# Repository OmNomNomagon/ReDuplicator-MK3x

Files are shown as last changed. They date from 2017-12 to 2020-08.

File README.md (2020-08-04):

This project is a complete overhaul of the original Wanhao i3 with a few main objectives:
- Keep the core components of the printer while upgrading its structure.  
- Create maximum rigidity through a sturdy 3030 Aluminium extrusion frame. 
- Allow for future proofing and commonality of parts by basing all printed parts on the current Original Prusa MK3 files. 
- Reduce the weight of the X and Y carriages where possible to improve print speed and quality.

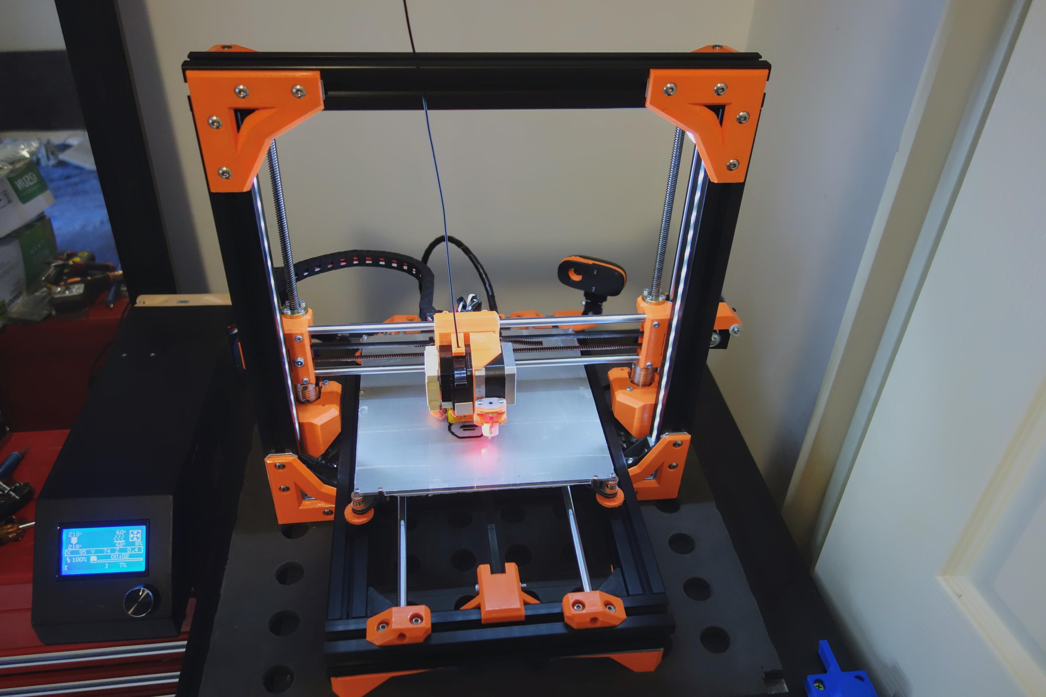
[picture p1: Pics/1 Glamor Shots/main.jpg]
noooice
 

The Wanhao i3 is a fabulous printer, but new generations of printers have begun pushing the boundaries. It has become apparent that in comparison, the Wanhao has a few deficiencies. Deficiencies which we will address in this project. The key improvements of this upgrade include:
- Much better rigidity through 3030 extrusions and metal brackets. Even with my or Azza’s excellent z braces the printer was still susceptible to slight wobble, especially under twisting forces (pull left tower and push right tower). When moving the printer it would require constant releveling due these small movements. Now i can barely get any movement using my full strength. 
- Comfortably increase Z height to ~200mm
- Reduce noise. By not screwing the motors directly onto the metal frame, motor vibrations and noise is reduced significantly. 
- Move towards more standard Prusa files for future upgradability, but with added strength improvements.
- Modular hotend, This design allows for the hotend to be replaced easily replaced without disassembling the printer. I have created a Titan Aero mount as an alternative to the original MK10 with a E3DV6 mount incoming.
- Sturdier 4 bearing Prusa style X-gantry. Not sure if it was specific to my printer or a common Wanhao problem, but my X gantry always had a lot of wobble which may have been a source of printing artifacts.  
- Noticeably better print quality due to a combination of everything above. I am able to print faster with better quality.
- All Wanhao i3 variants and rebrands are compatible, however the plus will require additional work to create an enclosure for the electronics. This project can also be built from scratch, or salvaged from other printers as long as measurements are altered accordingly. 

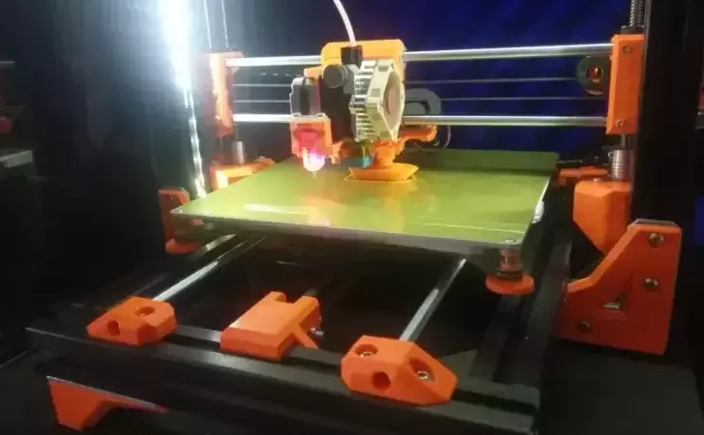
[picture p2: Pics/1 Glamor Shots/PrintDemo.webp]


Sample Print @~100mm/s on the titan aero extruder.

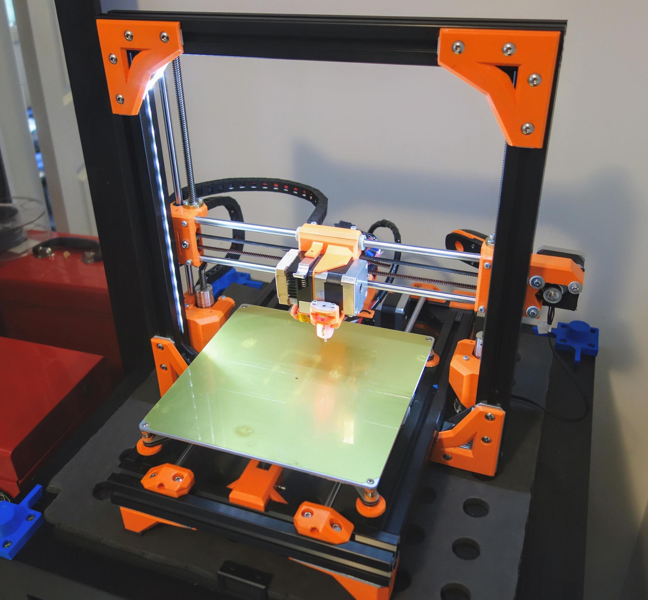
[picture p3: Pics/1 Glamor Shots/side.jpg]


Sample of improved print quality. 0.24mm layer height @ 70mm/s (titan aero).

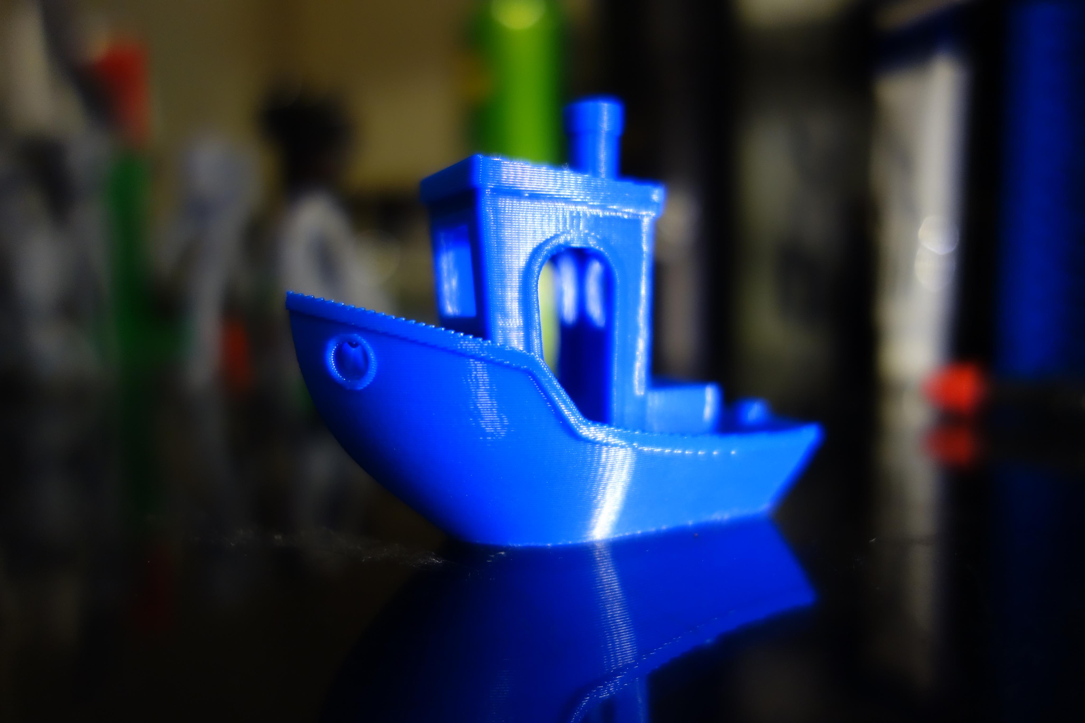
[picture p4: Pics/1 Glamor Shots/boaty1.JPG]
boatyMcboat


This project will be maintained both at [github](https://github.com/OmNomNomagon/ReDuplicator-MK2sx) and at [thingiverse](https://www.thingiverse.com/thing:2686588). The files were created using a combination of Fusion360 and tinkercad. They can be viewed and edited via [this Tinkercad link.](https://www.tinkercad.com/things/azPlfmHU5MQ#/)  

## Table Of Contents

- [1. Bill Of Materials](https://github.com/OmNomNomagon/ReDuplicator-MK2sx/wiki/1.--Bill-Of-Materials)
- [2. Printing Parts & Pre Assembly](https://github.com/OmNomNomagon/ReDuplicator-MK2sx/wiki/2.-Printing-Parts-&-Pre-Assembly)
- [3. Base](https://github.com/OmNomNomagon/ReDuplicator-MK2sx/wiki/3.-Base)
- [4. Begin The ZTower](https://github.com/OmNomNomagon/ReDuplicator-MK2sx/wiki/4.-Begin-The-ZTower)
- [5.1 Hotend MK10 Original](https://github.com/OmNomNomagon/ReDuplicator-MK2sx/wiki/5.1-Hotend-MK10-Original)
- [5.2 Hotend Titan Aero Upgrade](https://github.com/OmNomNomagon/ReDuplicator-MK2sx/wiki/5.2-Hotend-Titan-Aero-Upgrade)
- [5.3 Hotend E3D Hemera Upgrade](https://github.com/OmNomNomagon/ReDuplicator-MK3x/wiki/5.3-Hotend-Hemera-upgrade)
- [6. XAxis Gantry](https://github.com/OmNomNomagon/ReDuplicator-MK2sx/wiki/6.-XAxis-Gantry)
- [7. Complete the ZTower](https://github.com/OmNomNomagon/ReDuplicator-MK2sx/wiki/7.-Complete--the-ZTower)
- [8. YAxis](https://github.com/OmNomNomagon/ReDuplicator-MK2sx/wiki/8.--YAxis)
- [9. Cabling](https://github.com/OmNomNomagon/ReDuplicator-MK2sx/wiki/9.-Cabling)
- [9.1. Recommendations & Future Dev](https://github.com/OmNomNomagon/ReDuplicator-MK2sx/wiki/9.1.-Recommendations-&-Future-Dev)

## Thanks and Acknowledgements
- [Prusa Research MK2s](https://github.com/prusa3d/Original-Prusa-i3) 
- [Datvr's Prusa MK2S-x](https://www.thingiverse.com/thing:1692666)
- [Thorped's excellent Wanhao Fan Duct ](https://www.thingiverse.com/thing:1246425)
- [Cyul's spool holder](https://www.thingiverse.com/thing:1635585)

## Changelog
1.0 - Initial Release

1.01 - Updated idler files with multiple z endstop mount points for upcoming Titan Aero upgrade. Sturdier cable cover box. Added 1Meter GT2 belt to BOM as the stock belt may not be long enough (can anyone confirm?)

1.02 - Updated the **Part Fan Bracket** to **Part Fan Bracket V1.1** The original doesn't align with the carriage plates properly. Please print the revised one.

1.03 - Uploaded a new Y Carriage Belt Holder. This one is based on the current MK3 design and is much easier to fix and tension.

1.04 - **X Gantry Idler 9MM V2** was missing the heat-sert insert holes to mount the cable box. Updated and fixed with **X Gantry Idler 9MM V3**. If you have already printed V2, you can keep the part and manually drill 2x 4mm holes spaced 9mm wide and 6mm deep.

1.1 - 11/03/2018 Major Prusa MK3 Update. This updates an update of many of the original MK2s based parts to MK3 Based parts. This includes;

  - MK3 Based Part Cooling shroud and mount. It performs much better than the original Thorped based one. flawless @60 degree overhang with some sagging @70 degree overhang. The original would show artefacts [@60 degrees.](https://raw.githubusercontent.com/OmNomNomagon/ReDuplicator-MK2sx/master/Pics/9%20Titan/overhang.jpg). Almost comparable to the [Dii Cooler.](https://www.reddit.com/r/3Dprinting/comments/7kexdv/a_nearly_comprehensive_study_of_cooling_fans_and/) 

  - Much improved X Carriage. This uses the new [MK3 belt mounting method](https://raw.githubusercontent.com/OmNomNomagon/ReDuplicator-MK2sx/master/Pics/4%20Hotend/CarriageNew.jpg) which is much easier to install under tension. The whole extruder assembly can now also easily slide on and off the rods to greatly simplify installation and maintenance. 16mm M3 screws are used to secure the bearings. I've also made and tested changes which allow the extruder assembly to be built without heat-serts and can be substituted with M3 nylocks. NOTE: due to these changes the Rear carriage plate is NOT compatible with the existing Front extruder plate as the hole spacing has been changed. The New Front extruder plate must be used.

  - Front Extruder Plate. Better spacing around the hotend to improve the filament path. Updating Hole Spacing to be compatible with the new Rear Carriage Plate. Strengthened BLTouch mount. Increase spacing around heater block to reduce residual heat. Not compatible with old extruder plate.

  - X Axis Motor Mount. Incorporates the new MK3 design. Better Spacing to ensure a straighter belt path. Includes new MK3 tensioner to easily tension X belt. Requires M3nS Nut and 20mm M3 screw. (Enough tension can be applied by without the M3nS) Installation is similar to the Prusa instructions [here, steps 11-18.](http://manual.prusa3d.com/Guide/4.+Z-axis+assembly/509?lang=en)

  - As this project  contains dozens of files already, Older retired files are retired to the [Retired Versions directory in github](https://github.com/OmNomNomagon/ReDuplicator-MK2sx/tree/master/STLs%20Reduplicator%20Core%20Parts/Retired%20Versions)
  
1.1.1 - Endstop Part For sensorless homing with TMC2130 Drivers.

1.2 - 05/11/2018 - Multiple improvements based on Prusa MK3 R3 release. This includes:

  - Prusa MK3 R3 based part cooling shroud. This gives a noticeable improvement over the original shroud. Also improved the clearance between the shroud and the nozzle.

  - Improved X Carriage rear plate. This was strengthend to better handle bumps and knocks. Rigidity is also improved. It is still a common part between the MK10 and titan aero extruders. 

  - Strengthened Z Rod Securer parts. Some people had issues with these snapping in PLA but should no longer be an issue.

1.3 - 17/02/2020 - E3D Hemera mount. Updated fan duct to the most recent R4 release. Added an angle for increased rear fan duct clearance. This will filter down to the other hotend designs shortly. Initial update of parts across to fusion 360. A number of parts have been converted and this will continue over time.

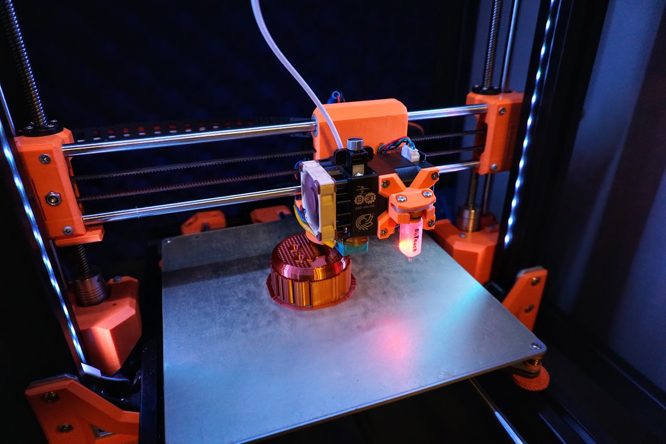
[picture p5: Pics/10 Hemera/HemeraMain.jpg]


Improved cable mounting system by clipping onto the X axis motor

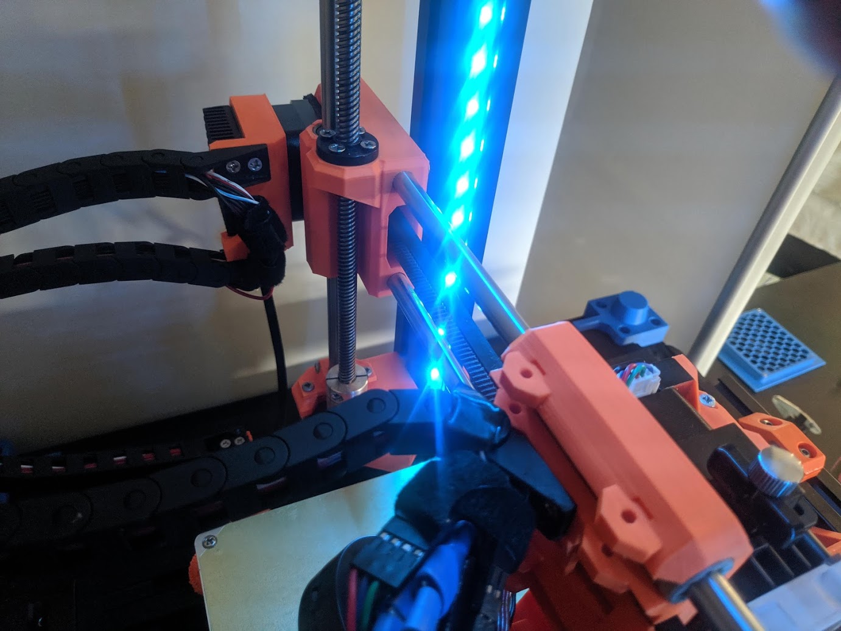
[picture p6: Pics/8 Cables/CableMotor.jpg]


1.3.1 - 19/02/2020 - MK52 Removeable heatbed Mod - resized rods and extrusions to accommodate the prusa MK3 heatbed.

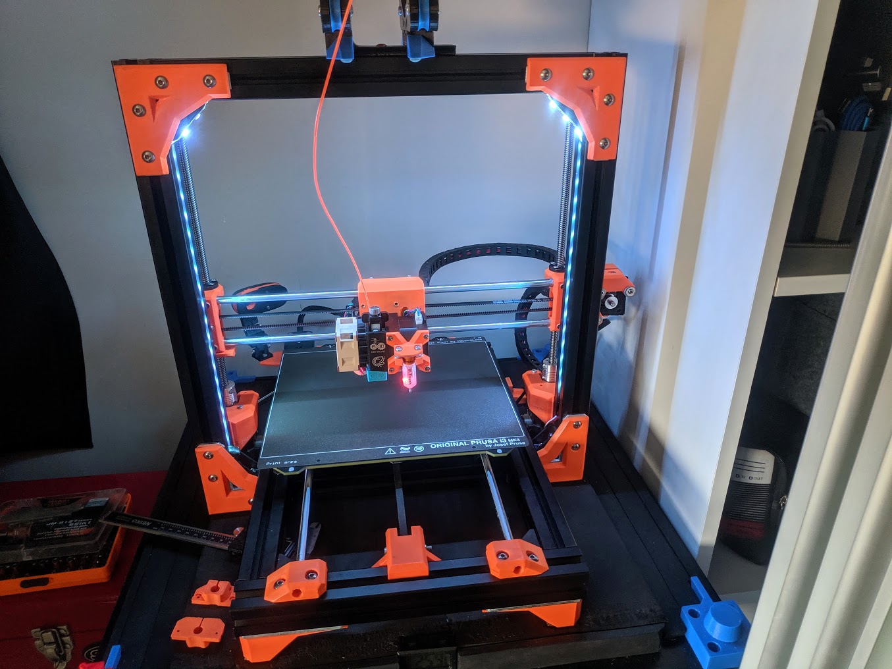
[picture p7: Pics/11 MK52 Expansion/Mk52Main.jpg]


1.4 - 05/08/2020 - Mk52 and Hemera Parts update. Significantly improved X idler, tensioner and motor holder, new Z Rod Holder design for much easier installations and accuracy. Improved Hemera fan shroud with improved airflow. Continued conversion from tincercad to F360 parts. These changes will filter down to the original reduplicator parts.

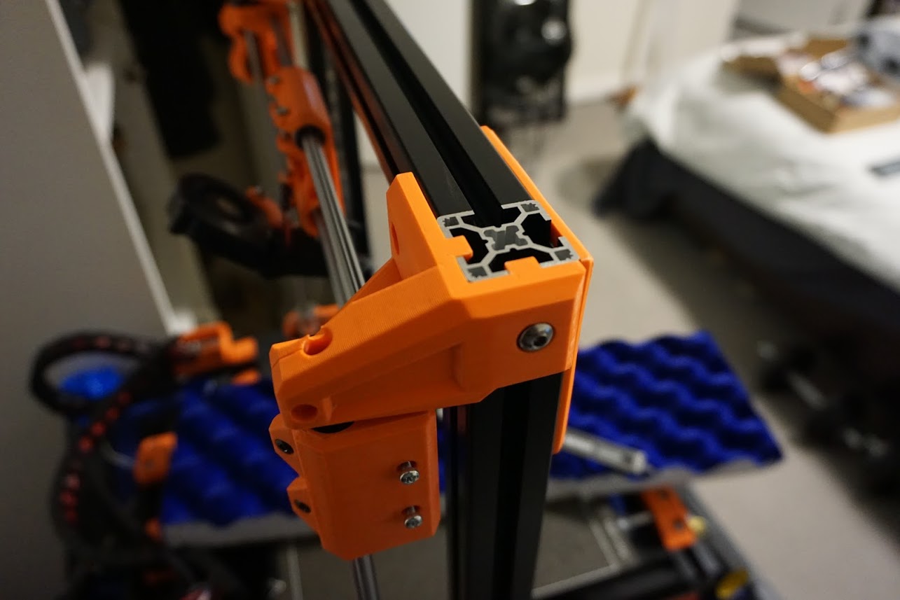
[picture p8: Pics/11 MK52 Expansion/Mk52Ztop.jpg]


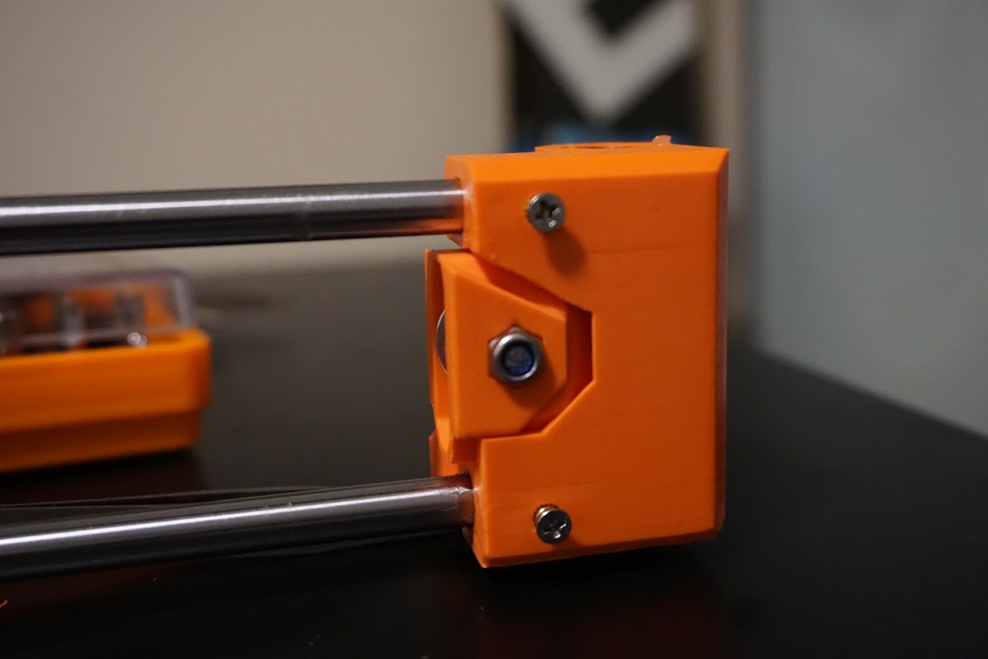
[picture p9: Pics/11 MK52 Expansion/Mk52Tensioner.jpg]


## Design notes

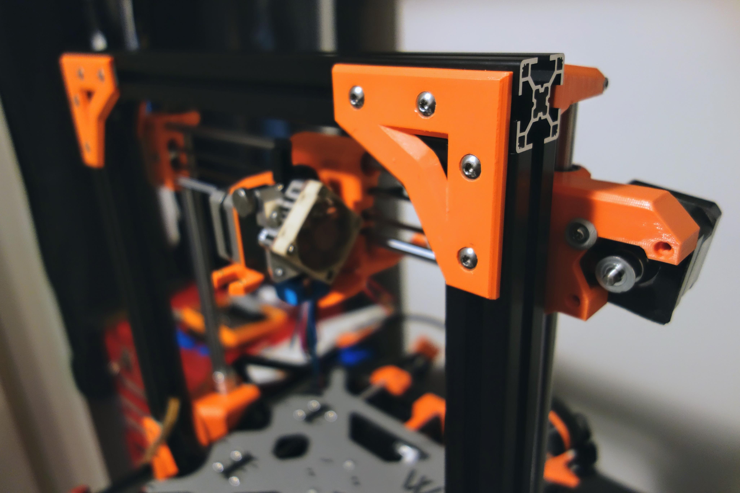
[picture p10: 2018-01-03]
Pics/5 Gantry/XGantryMotor.JPG

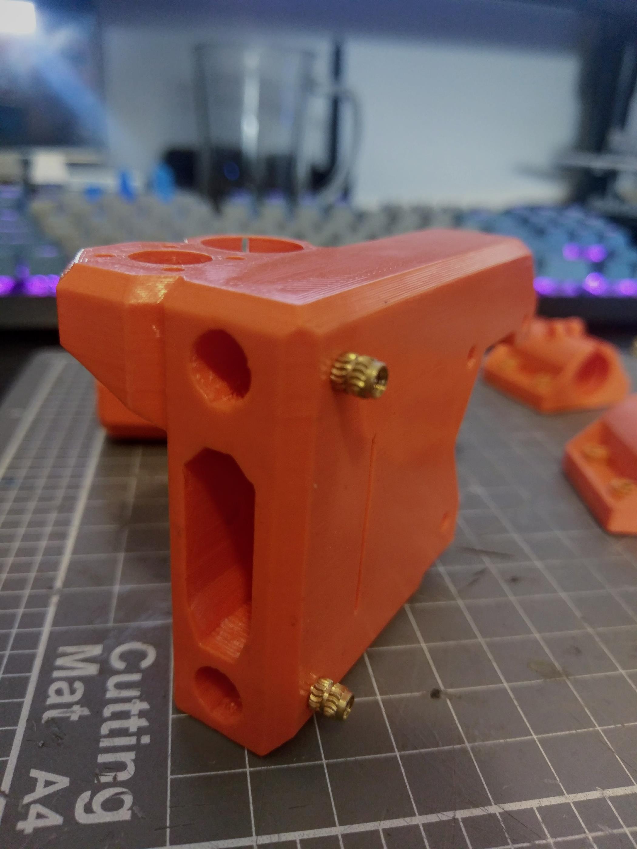
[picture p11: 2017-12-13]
Pics/5 Gantry/HeatSert1.jpg

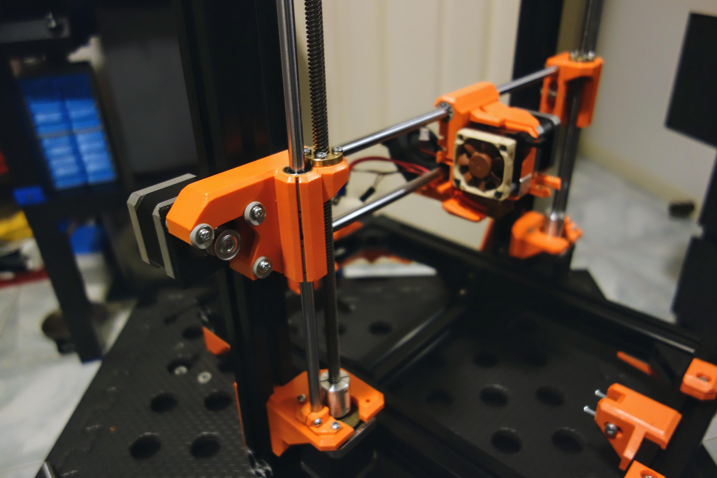
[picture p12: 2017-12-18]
Pics/1 Glamor Shots/ReversedEG.JPG

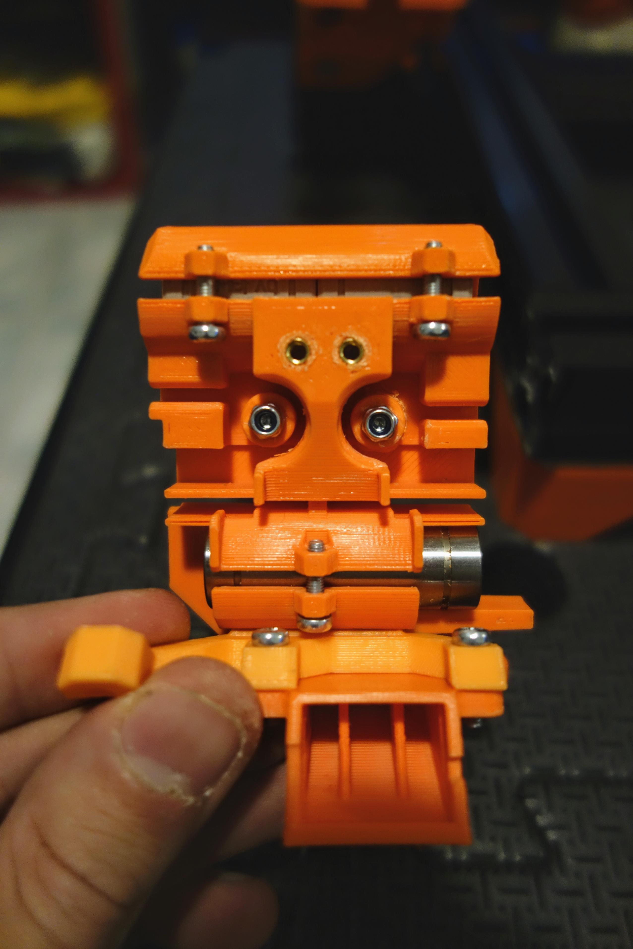
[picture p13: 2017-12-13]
Pics/4 Hotend/Fan2.jpg

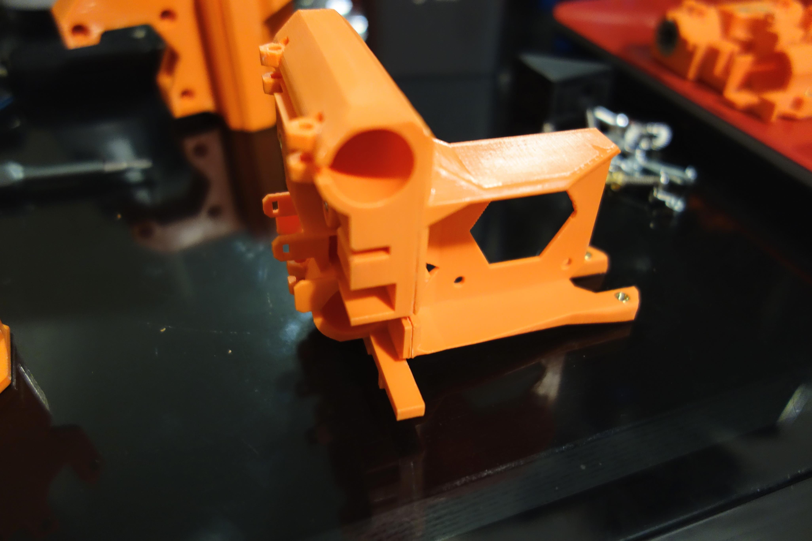
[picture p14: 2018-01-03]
Pics/9 Titan/TitanPart.JPG

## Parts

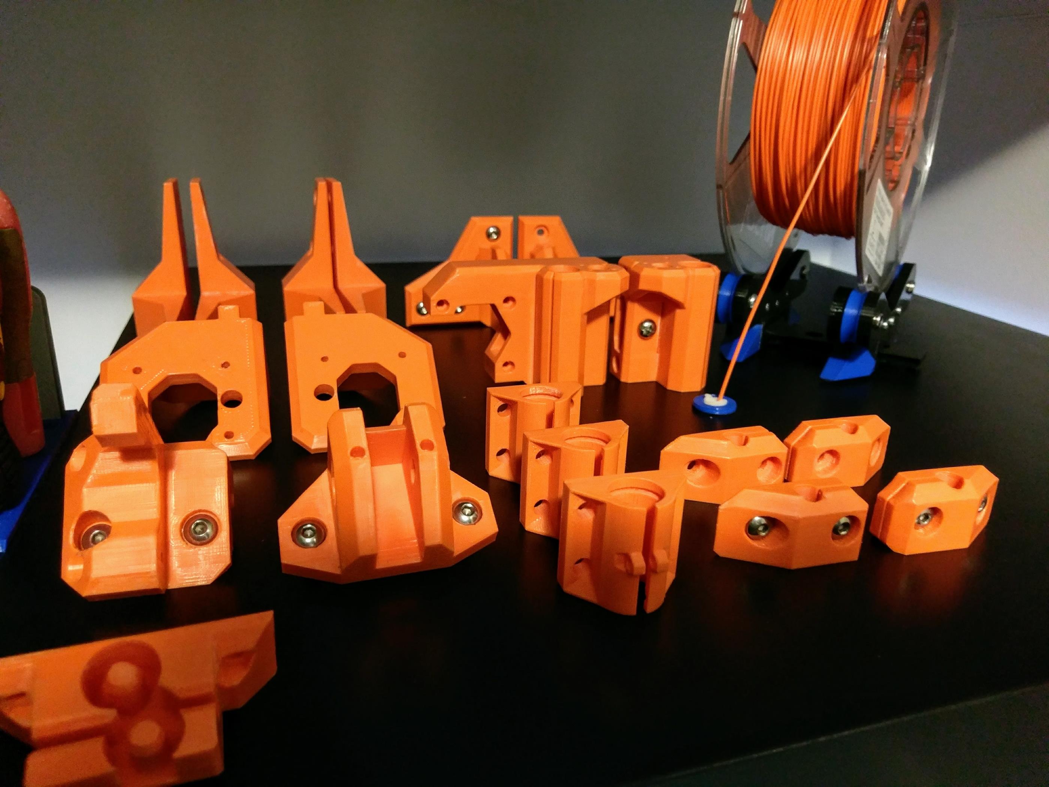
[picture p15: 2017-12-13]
Pics/2 Bottom Frame/Parts.jpg

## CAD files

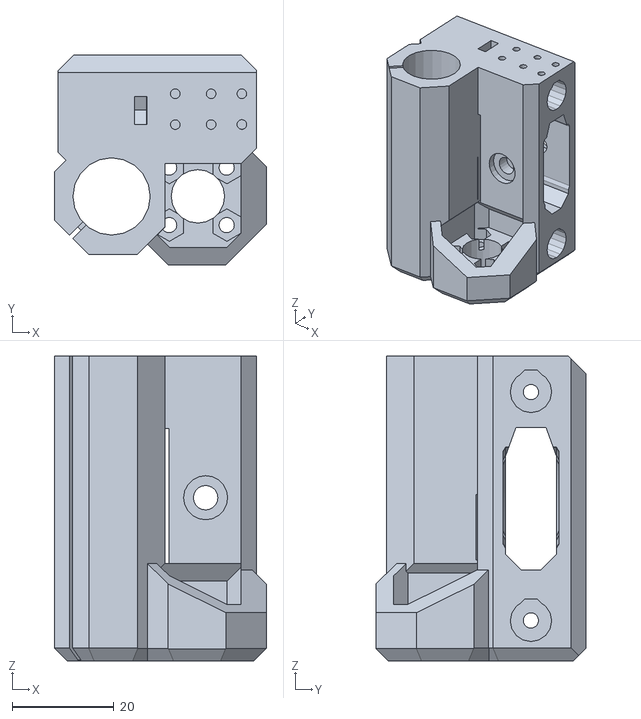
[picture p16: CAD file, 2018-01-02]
STLs Alternative & Optional/X Gantry Idler 11mm (Stock idler) V2.stl
41.7 x 41.4 x 60.0

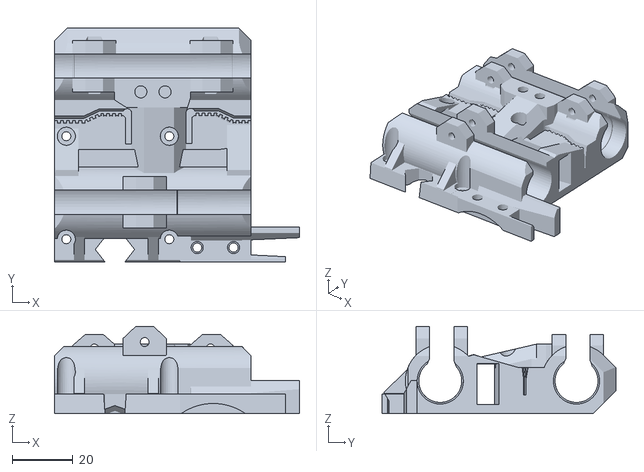
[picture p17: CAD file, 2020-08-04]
STLs E3D Hemera Hotend upgrade/Hemera X Carriage 360 V2.stl
80.9 x 77.2 x 28.8

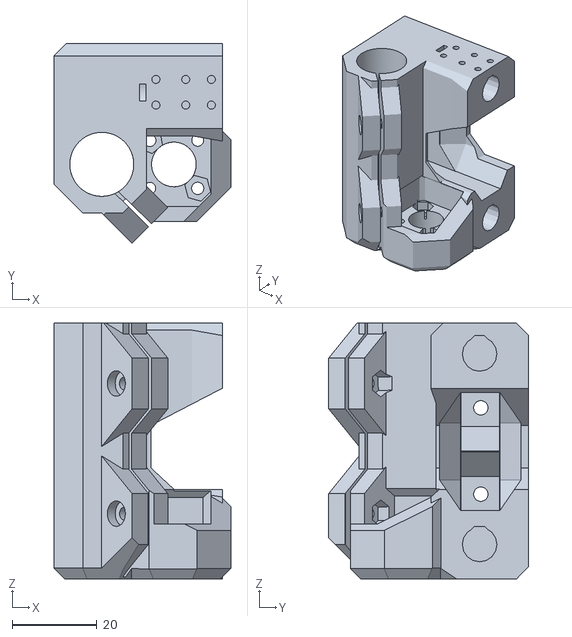
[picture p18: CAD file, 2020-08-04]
STLs MK52 Heatbed Expansion Upgrade/X Gantry Idler - MK52 Expansion 360 v2.stl
41.7 x 47.1 x 60.5

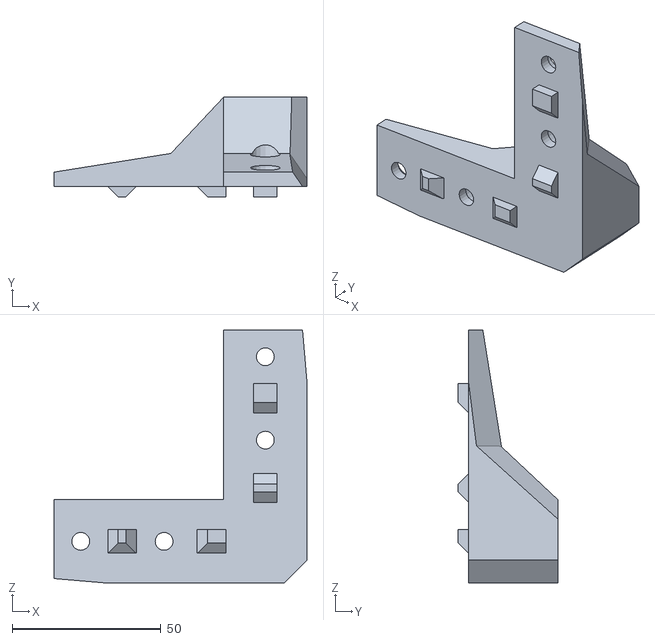
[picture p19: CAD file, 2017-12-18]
STLs Non Metal Tabbed Brackets/Leg H30.00 - Non Metal Tabbed X4.stl
85.0 x 33.5 x 85.0

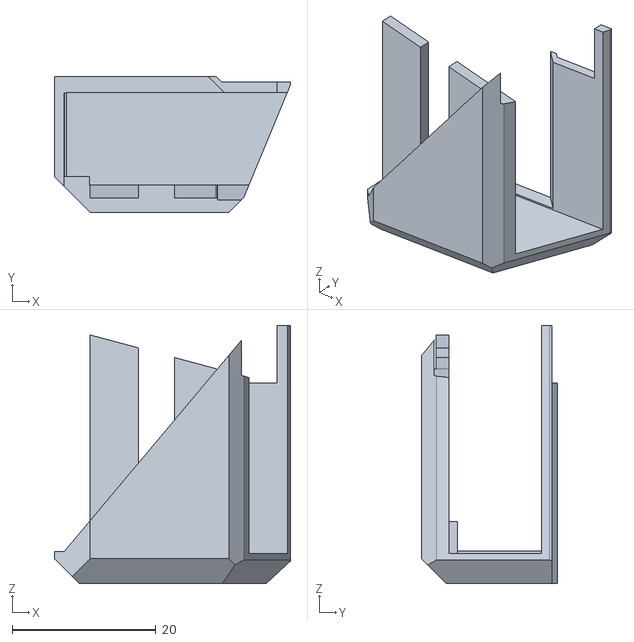
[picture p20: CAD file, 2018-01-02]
STLs Reduplicator Core Parts/Alternative Parts/X Gantry Cable Box Cover V2.stl
32.9 x 18.9 x 35.9

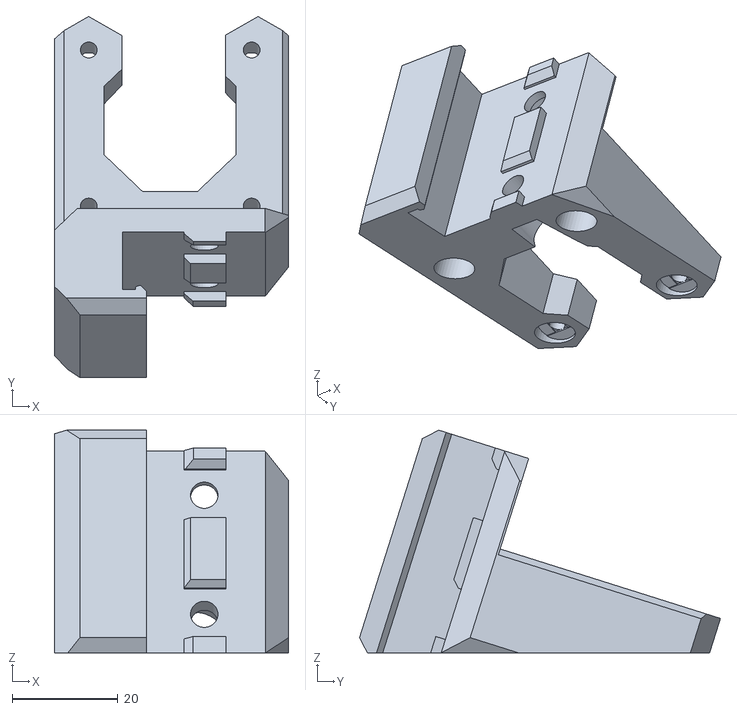
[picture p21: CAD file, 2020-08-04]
STLs Reduplicator Core Parts/Y Axis Motor Mount V3 360.stl
44.4 x 68.4 x 42.2

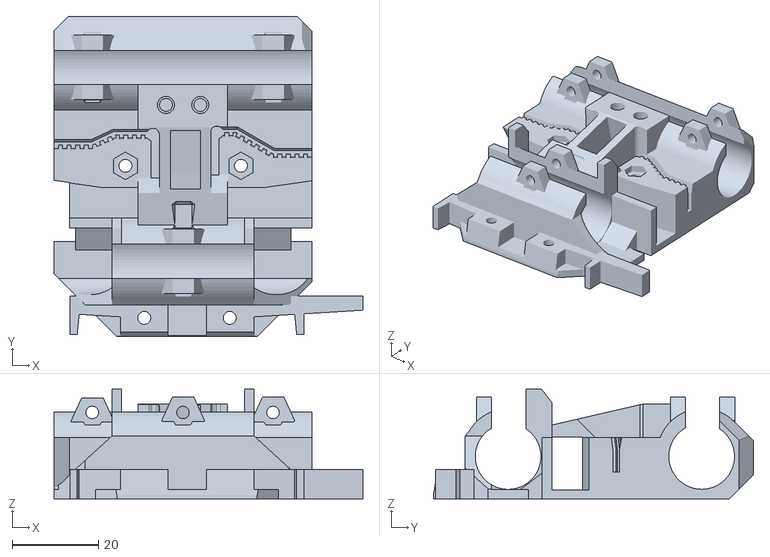
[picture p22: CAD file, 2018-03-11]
STLs Titan Aero Conversion/X Carriage Rear Bearing Plate MK3 V2.stl
71.8 x 74.4 x 25.5

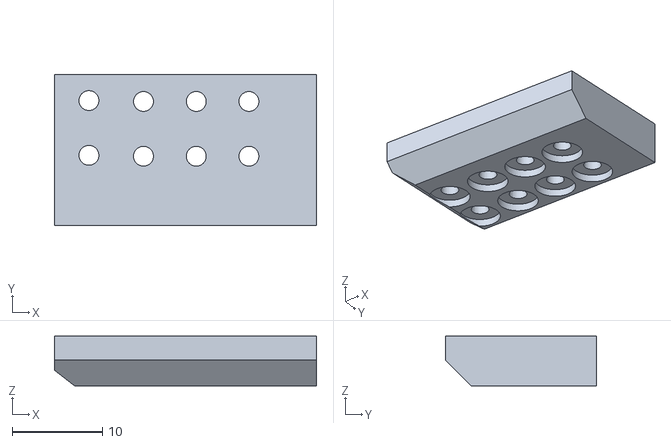
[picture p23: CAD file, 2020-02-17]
STLs Titan Aero Hotend Upgrade/X Axis TMC2130 Sensorless Endstop 360.stl
29.0 x 16.7 x 5.50

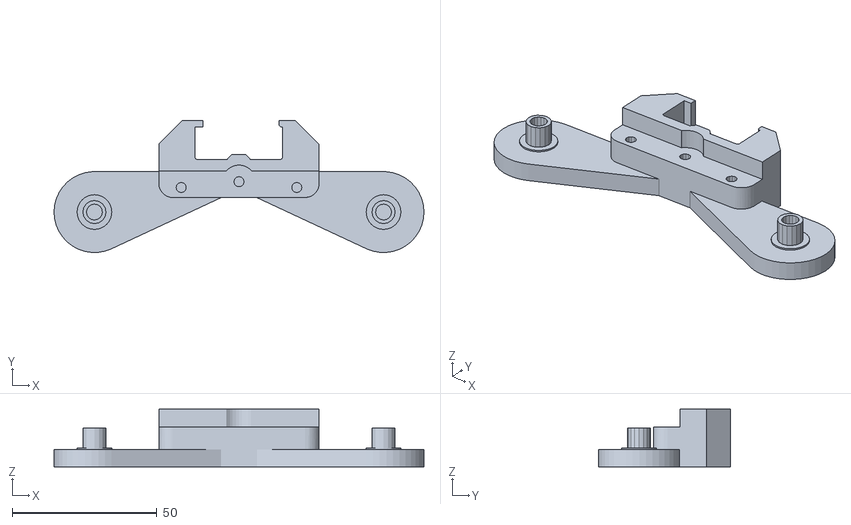
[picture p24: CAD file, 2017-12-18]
STLs Alternative & Optional/Top Mount Spool Holder Right.stl
128.0 x 45.6 x 20.0

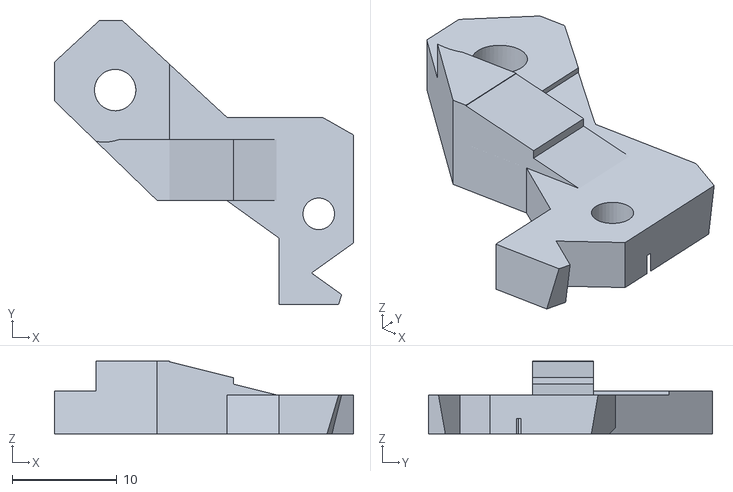
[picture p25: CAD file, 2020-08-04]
STLs E3D Hemera Hotend upgrade/Hemera Fan Mount V2 360.stl
28.6 x 27.1 x 6.93

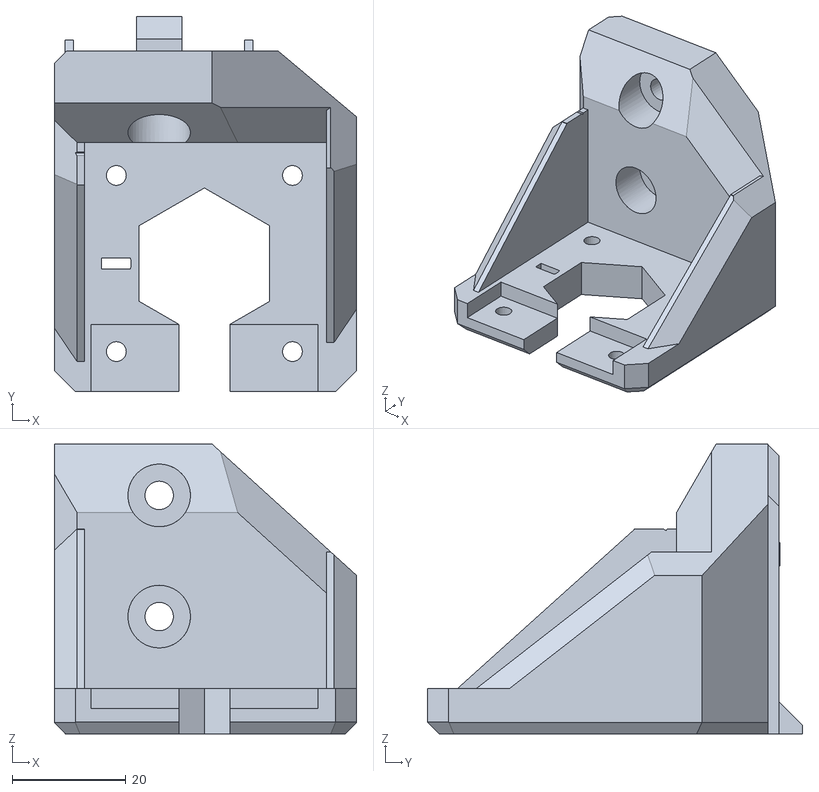
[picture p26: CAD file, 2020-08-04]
STLs MK52 Heatbed Expansion Upgrade/Z Axis Motor Bottom Left - MK52 Expansion 360 v2.stl
53.2 x 66.0 x 51.0

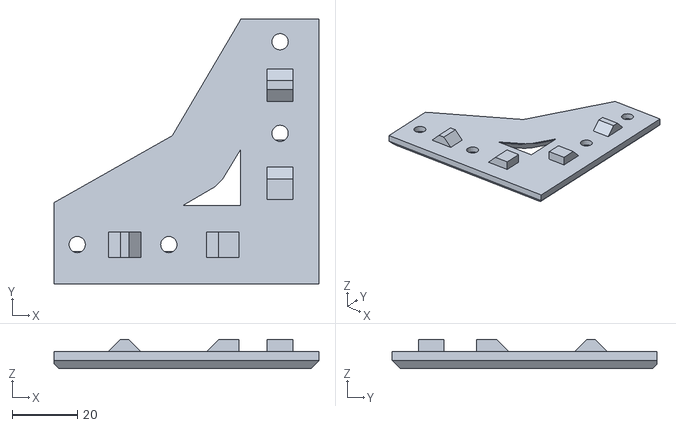
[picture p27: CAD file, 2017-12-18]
STLs Non Metal Tabbed Brackets/Tower Corner Bracket Large 80x80x5 V1 - Non metal Tabbed X2.stl
81.0 x 80.9 x 8.90

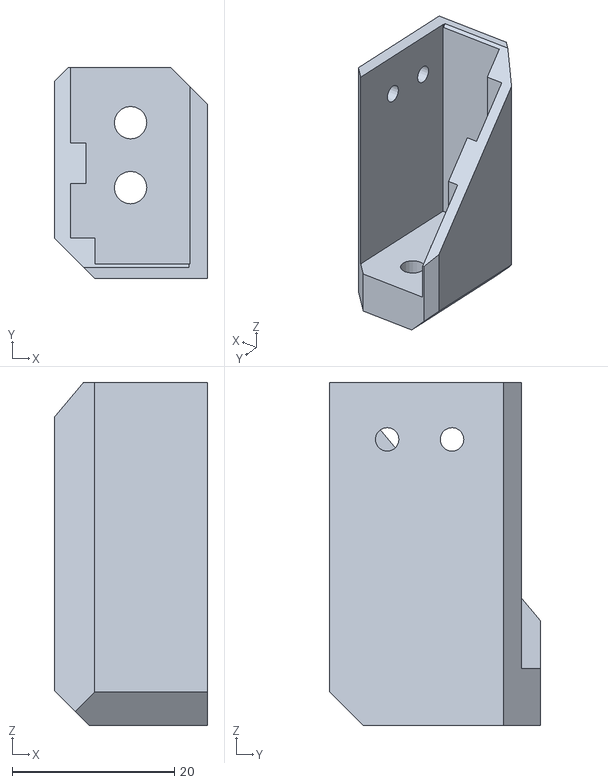
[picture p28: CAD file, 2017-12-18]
STLs Reduplicator Core Parts/Alternative Parts/X Gantry Cable Box Bottom.stl
18.9 x 26.0 x 42.3

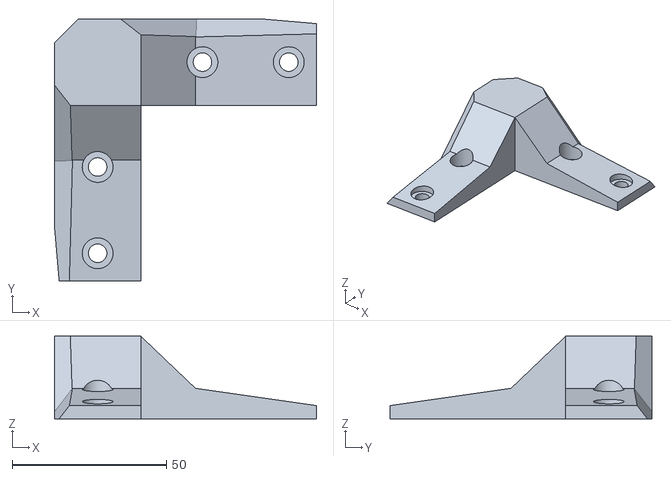
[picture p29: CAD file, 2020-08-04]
STLs Reduplicator Core Parts/Base Leg X4 360 V2.stl
85.0 x 85.0 x 26.8

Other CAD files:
STLs Titan Aero Conversion/Titan Aero MK3 Part Cooling Fan Shroud.stl
STLs Titan Aero Hotend Upgrade/Titan Aero MK3 Part Cooling Fan Mount V3.stl
STLs Alternative & Optional/Cable Chain Wiring Bracket Alternate.stl
STLs E3D Hemera Hotend upgrade/Hemera Fan Shroud R4 360 V2.stl
STLs Alternative & Optional/Cable Chain Wiring Brackets.stl
STLs Alternative & Optional/Control Box PTFE Filament Guide.stl
STLs Alternative & Optional/Corner Bracket Large 76x76x5 (Bunnings Alternate).stl
STLs Alternative & Optional/Corner Bracket Med 65x65x5.stl
STLs Alternative & Optional/Extrusion Extensions.stl
STLs Alternative & Optional/Top Mount Filament Guide .stl
STLs Alternative & Optional/Top Mount Filament Locking Ring PTFE 3MM OD & Cleaner.stl
STLs Alternative & Optional/Top Mount Spool Holder Left.stl
STLs E3D Hemera Hotend upgrade/Hemera BlTouch 360.stl
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

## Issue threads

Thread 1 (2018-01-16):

X Gantry Cable Box Bottom Poor Side Wall Extrusion

safetychief8, 2018-01-16:
There's poor extrusion in the walls of the X gantry cable box bottom. I loaded into S3D, and output the gcode file. The other items are printing without issue. Please check to see if there's an issue with the code. Tried to print it 3 times with tweaks in the settings, but had the same result.  Also, you show various washers in the pictures, but you don't mention them in the bill of materials. Are washers necessary?

OmNomNomagon, 2018-01-17:
In S3D what are your thin wall behavior settings?
I've got it setup as:

External Thin Wall: Perimeters Only
Internal Thin Wall: Allow Gap Fill
Allowed Perimeter Overlap: 20%

Dan you give me a more detailed description or a pic? Does it show up in the layer previews? I checked, it looks okay in mine but If it persists I'll bump the wall thicknesses by 0.5mm, which should fix it up.

With regards to washers, the only part that may need them is the X motor mount, and only if you use neoprene washers to try to decouple the motor from the frame. I'll update the wiki to clarify.

safetychief8, 2018-01-17:
Hello,

With regards to printing, it only seems to be that one part for some reason, all the others print fine, that's why I suggested that that code or print settings may be suspect. I'll look to purchase the washers for the appropriate sized screws, thanks.

Sent via the Samsung Galaxy S8, an AT&T 4G LTE smartphone

-------- Original message --------
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

safetychief8, 2018-01-19:
I've attached some pictures of the extruded part.

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

OmNomNomagon, 2018-01-21:
Oh wow, don't think its an issue with the file. Is this PETG? It looks like maybe you need to dial up the temps a bit and maybe increase your extrusion modifier a tad.

safetychief8, 2018-01-22:
It’s PLA, all the other parts extruded ok with the same material and settings.

Sent from my iPad

On Jan 21, 2018, at 9:16 AM, OmNomNomagon <notifications@github.com<mailto:notifications@github.com>> wrote:

Oh wow, don't think its an issue with the file. Is this PETG? It looks like maybe you need to dial up the temps a bit and maybe increase your extrusion modifier a tad.

—
You are receiving this because you authored the thread.
Reply to this email directly, view it on GitHub<https://nam02.safelinks.protection.outlook.com/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>, or mute the thread<https://nam02.safelinks.protection.outlook.com/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>.

OmNomNomagon, 2018-01-22:
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

I printed another one out super quick with no issues.
Id say this is an issue with your printer that is only showing up on parts with thinner or finer details. I used to have a similar problem with certain types of petg. Without knowing more about your setup, reckon you should check the following.
- Double check your extruder drive gear is not loose or clogged,
- is your fan aimed to high? if the part fan is cooling your heater block it could cause these sorts of issues. Try reducing fan speed.
- double check your esteps https://3dprinterwiki.info/extruder-steps/
- retraction might be too high, causing melted plastic to move too far past the heatbreak, It would cause issues specifically on thinner prints with more retractions. try reducing this.
- Bump up your temperature
- Bump up your extrusion multiplier
- might just be bad or inconsistent filament

Please let me know if you have any luck with this.

safetychief8, 2018-01-23:
Thanks, I'll try them, just set up the Maker V2, I'll try it on that printer instead of the delta.

Closed 2018-01-29.

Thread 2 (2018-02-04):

Bill of materials missing M5 washers

MarMed, 2018-02-04:
I believe the Bill of materials is missing the M5 washers needed for the X and Y idlers, unless they are pulled from somewhere on the Wanhao.

OmNomNomagon, 2018-02-06:
Yes, you are completely correct, I'll update the BOM.

OmNomNomagon, 2018-02-09:
Updated, thanks for the heads up.

Closed 2018-02-09.

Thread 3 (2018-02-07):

Y carriage base

maltitco, 2018-02-07:
Where I can find a dxf and information from which material to cut Y carriage base?

OmNomNomagon, 2018-02-09:
The Y carriage plate was carried over from the original Wanhao. My particular plate was a lighter aftermarket on as the original was prone to warping. it was purchased via http://tehnologika.net/ although the site appears to be down at the moment. It is an Alu Melamine composite. Any Wanhao compatible Y-plate will work. There are a number of alternatives.

Here is a dxf source.
https://www.thingiverse.com/thing:1708260

If cutting from aluminium a thickness of 3mm - 4mm should give you the desired stiffness at the lowest weight.

Closed 2018-02-09.

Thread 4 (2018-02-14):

Titan Aero part Cooling Fan Mount.stl has too thin walls

MarMed, 2018-02-14:
Titan Aero part Cooling Fan Mount.stl has too thin walls where the heat serts holes are, resulting in a slicing error.

OmNomNomagon, 2018-02-15:
Okay, I'll take a look

OmNomNomagon, 2018-02-18:
It appears at some points the walls are too thin to print with a .4mm nozzle, however the part is still strong and functional and still accepts the heat serts. I'll try to redesign this part but this area in particular is very narrow and may not be possible

OmNomNomagon, 2018-03-11:
New MK3 Fan shroud has been uploaded :) . It has much better spacing in this area, by incorporating the shroud and bracket into one.

Closed 2018-03-11.

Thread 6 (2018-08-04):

Y-carriage bearing blocks are not listed under the 'multiple copies required' summary in section 2

ddcunningham, 2018-08-04:
The Y carriage bearing block STL only has one Y carriage included in it, but is not listed under the 'multiple parts required' summary.  If one follows sections 1 and 2, they will be short 2 bearing blocks.

OmNomNomagon, 2018-08-09:
thanks mate, wiki has been updated.

Closed 2018-08-09.

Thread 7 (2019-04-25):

BOM missing M2 heat-serts for Y Axis Idler?

beriberikix, 2019-04-25:
[Section 3.](https://github.com/OmNomNomagon/ReDuplicator-MK3x/wiki/3.-Base) states that the  Y Axis Idler needs 2x M2 heat-serts inserted on the front. I haven't built this yet but if that's correct, should M2 heat-serts be added to the [BOM](https://github.com/OmNomNomagon/ReDuplicator-MK3x/wiki/1.--Bill-Of-Materials)?

OmNomNomagon, 2019-06-26:
Thanks for bringing this up. its a spelling mistake. These parts are M3 heatserts and are already included in the bom total. I've updated the pages.

Closed 2019-06-26.

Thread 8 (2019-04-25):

BOM missing M3ns for X Gantry Motor Mount MK3 V2?

beriberikix, 2019-04-25:
[Section 7.](https://github.com/OmNomNomagon/ReDuplicator-MK3x/wiki/7.-Complete--the-ZTower) states that the X Gantry Motor Mount MK3 V2 needs a M3ns, though the changelog says it is optional. I haven't built this yet but if that's correct, should a M3ns be added to the [BOM](https://github.com/OmNomNomagon/ReDuplicator-MK3x/wiki/1.--Bill-Of-Materials)?

OmNomNomagon, 2019-06-26:
Thanks mate, i added them to the BOM. I skipped over them originally as I couldn't source these parts.

Closed 2019-06-26.

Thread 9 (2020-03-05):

Assembling the fan with the titan aero extruder

pgrandin, 2020-03-05:
I am having some issues figuring out how to properly assemble the fan shroud onto the X carriage backplate. I somewhat got it to hold but it's dangling a bit and it's often scratching my prints causing issues.

The wiki at https://github.com/OmNomNomagon/ReDuplicator-MK3x/wiki/5.2-Hotend-Titan-Aero-Upgrade says
> Use 2 16mm M3 screws through the bottom x carriage screw holes and into this part.

It does not mention if we should use nuts on one side, or from which side the screws should be inserted (I think that it is from the direction in the screenshot below as otherwise the intake is blocking the path of one of the screw).

Using 16mm screws without nuts doesn't really hold the shroud in place, but on the shroud there is no hole shaped like a nut to help secure it in place, and it is quite difficult to insert one there and hold it in place.

What is the right way to do it? This section view should help visualize the issue i'm facing.

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

 - orange : Titan Aero X Carriage Front Plate MK3 V2
 - white : Titan Aero MK3 Part Cooling Fan Shroud MK3 R3
 - grey : X Carriage Universal Rear Bearing Plate MK3 V3

The 2 screws are M3x12, screwed into the heatsearts (in gold color)

Thank you for sharing this project. You have done an amazing work.

OmNomNomagon, 2020-03-06:
Great visualization. After this version I realized that this design was over constrained. The best bet is not to have heat-serts in the extruder plate (purple) but to only have them in the fan shroud. Then screw in as you have done here with 16-20mm M3 screws. This should pull everything together tightly.

pgrandin, 2020-03-06:
Makes sense!
Thank you!

Closed 2020-03-06.

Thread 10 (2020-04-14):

BOM clarity?

rogerschlachter, 2020-04-14:
Found my way here after doing some upgrades to my Wanhao i3+ (Hemera, Duet wifi, etc).  Pretty awesome project! Thank you so much for documenting everything you have and providing all of the STLs in a single pretty easy to find place.

I know it might be difficult to do, but would it be possible to clear up the BOMs a little?  For instance, I started going through what I'd need to build the Hemera version with the MK52 Heat Bed and things seem a little off?  For instance, the MK52 instructions say four bearings, but I see only three in the assembly of the bed, and I'd still need some for the X axis I imagine, vs say the extrusions where it tells me they replace the original parts. The MK52 instructions also leave off the Y idler part from the printed parts. And they mention hotend pieces so I'm not sure if it's trying to be all encompassing or just talk about the base parts?  It's just a little hard to get a clear picture of what I'll need. I don't want to disassemble my printer until I know I have everything I need printed.

Just wondering if there's maybe a better way to show the differences?  Maybe the table with all of the printed parts for the base version and a table with all of the purchased parts.  Then copy that same table into the altered builds and add a column for that option that says "Use Part X instead" or "Not used for this option".  Maybe something like this?

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

If the lists are clearer, I'd be up for coding up a little javascript to allow people to pick options and let it build a single list for them.

OmNomNomagon, 2020-04-24:
Thanks mate, sounds like a solid idea. I'll go through everything this weekend and clean it up

OmNomNomagon, 2020-05-18:
The 4 bearings mentioned in the instructions are for the x axis end. They are mentioned as they are additional parts required on top of the original wanhao parts. 2 bearings for into the X axis idler and 2 for the x axis motor mount. . The 3 heatbed carriage bearings and 2-3 x-carriage bears can be pulled accross from the original wanhao. Although you may as well upgrade them while doing this project. I'm going back through everything to ensure its all covered. I'll come up with a Full BOM just for the MK52 upgrade

Closed 2020-08-04.

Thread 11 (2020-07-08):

Corner bracket BOM clarity

Abai, 2020-07-08:
@OmNomNomagon  - Thank you for this awesome design! I am building it from scratch.

I have a few questions regarding the corner brackets:

1. *Should we use M5 or M6 corner brackets, screws and T-Nuts?*

 I noticed that you recommend Misumi [HBLFSNB6](https://uk.misumi-ec.com/vona2/detail/110300442340/?HissuCode=HBLFSNB6) and this part is for **M6** according to the [data sheet](https://uk.misumi-ec.com/pdf/fa/2014/P2_0585-0586_F40_EN.pdf), yet the T-Nuts in the BOM are **M5**. The M5 version of this bracket is [HBLFSN6-5](https://uk.misumi-ec.com/vona2/detail/110300442340/?PNSearch=HBLFSN6-5), but unfortunately it does not come black anodized, which is so pretty :) The recommended Misumi T-Nuts for both corner version are M6 [HNTT6-6](https://uk.misumi-ec.com/vona2/detail/110302610850/?HissuCode=HNTT6-6) and M5 [HNTT6-5](https://uk.misumi-ec.com/vona2/detail/110302610850/?HissuCode=HNTT6-5).

 So the options are:

 * 14 x [HBLFSNB6](https://uk.misumi-ec.com/vona2/detail/110300442340/?HissuCode=HBLFSNB6) (Black M6 double tabbed corners) and 28 x [HNTT6-6](https://uk.misumi-ec.com/vona2/detail/110302610850/?HissuCode=HNTT6-6) (M6 T-Nuts)
 * 14 x [HBLFSN6-5](https://uk.misumi-ec.com/vona2/detail/110300442340/?PNSearch=HBLFSN6-5) (Silver M5 double tabbed corners) and 28 x [HNTT6-5](https://uk.misumi-ec.com/vona2/detail/110302610850/?HissuCode=HNTT6-5) (M5 T-Nuts)

2. *Double or single tabbed corner brackets?*

 I see you recommend single tabbed corners, but the [HBLFSNB6](https://uk.misumi-ec.com/vona2/detail/110300442340/?HissuCode=HBLFSNB6) is double tabbed. If I understood correctly, I can use these corners without issue if I use Misumi T-Nuts, correct?

 Alternatively, we can use the single tabbed corners [HBLFSNK6](https://uk.misumi-ec.com/vona2/detail/110300442520/?HissuCode=HBLFSNK6) with non-Misumi T-Nuts. So we get a new possible option:

 * 14 x [HBLFSNK6](https://uk.misumi-ec.com/vona2/detail/110300442520/?HissuCode=HBLFSNK6) (Black M6 single-tabbed corners) and 28 x non-Misumi M6 T-Nuts

3. *Ok to use Misumi T-Nuts for non-corner joints?*

 I understand that non-corner joints have to be M5 because of the printed part dimensions, but do you think I can use the Misumi [HNTT6-5](https://uk.misumi-ec.com/vona2/detail/110302610850/?HissuCode=HNTT6-5) (M5 T-Nuts) here?

So my preferred BOM for corners, t-nuts and screws would be:

 * 14 x [HBLFSNB6](https://uk.misumi-ec.com/vona2/detail/110300442340/?HissuCode=HBLFSNB6) (Black M6 double tabbed corners)
 * 28 x [HNTT6-6](https://uk.misumi-ec.com/vona2/detail/110302610850/?HissuCode=HNTT6-6) (M6 T-Nuts)
 * 28 x M6 Screws (12mm)
 * 52 x [HNTT6-5](https://uk.misumi-ec.com/vona2/detail/110302610850/?HissuCode=HNTT6-5) (M5 T-Nuts)
 * 52 x M5 Screws (10 x 16mm, 42 x 12mm)

Thank you!

PS. I have also posted this question on Thingiverse, just in case.

Abai, 2020-07-13:
My preferred BOM should work. Find the detailed answer here: https://www.thingiverse.com/thing:2686588

Closed 2020-07-13.

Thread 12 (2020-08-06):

Printed parts don’t fit with Misumi T-Nuts

Abai, 2020-08-06:
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

The printed parts that attach to extrusions are tabbed. So are the Misumi T-nuts. The slots in the printed parts tabs, need to be 14mm wide, 7mm on each side of the screw hole center.

I saw that you created a new revision of parts two days ago. Very cool! I would like to fix these before reprinting. Could you please provide the fusion 360 files? This change should not cause any issues when using non-tabbed t-nuts like you do, so I can also make a pull request with fixed STL’s if you like.

Thanks!

Abai, 2020-08-06:
Alternative to making 14mm slots in printed tabs, it is possible to make all printed tabs 1mm high maximum. This is what misumi does with the tabs of gheir corner brackets.

Here are the drawings:

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

OmNomNomagon, 2020-10-18:
Hi mate, sorry you are having issues. M5 drop in T-nuts were always the preferred and recommended part for all the printed parts.  I recommend that you switch to drop in nuts for the printed parts and use the misumi ones for all the other structural parts.

Closed 2020-10-18.

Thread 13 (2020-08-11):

MK52 Expansion X Gantry measuremements

Abai, 2020-08-11:
On MK52 expansion wiki you mention:

“ The 380mm rods are mounted on the Y axis, 330mm rods on the z axis and 370 rods in the Y axis”

You mention Y twice here.

I assume 370 rod is for X gantry and 380 for Y axis.

If the above is correct, then the BOM table on the same page should also be updated.

OmNomNomagon, 2020-10-18:
Thanks Mate

you are correct, the lengths are:

new rods
x axis: 370mm
existing wanhao rods
Z Axis: 330mm
Y Axis: 380mm

Closed 2020-10-18.

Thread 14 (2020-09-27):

New Mk52 X Belt Tensioner

cpolera, 2020-09-27:
I'd like to make a suggestion. I would flip around the holes for the pulley holder for the x axis. Currently when you put the inserts into it they are on the side being pulled towards. This means they can be pulled out if they arent gripping well to the plastic. I'd also be concerned about it maintaining tension over time. If you could put them in from the opposite side, then they'll always be pulled towards the "center" of the printed piece with no risk of pulling through or slowly slipping out over time.

OmNomNomagon, 2020-10-18:
HI mate, this was my original idea, however i went through a dozen or so prototypes before settling on this design. To insert them from the other side would require making the side and top walls a little thinner, or moving the m3 screw holes closer together.

When the M3 holes were closer together I found it wasn't as stable. Making those walls thinner is also not an option as that is the current weak point in the design. I tested with overkill high torque steppers doing fast moves to stress the part. Every single time it would snap around the M5 bolt holding the idler well before pulling out the heat-sert.

I made a compromise to insert the heatserts from the back, in order to make the walls around the idler as thick as possible. Also I don't know if you've tried to remove heatserts from printed parts before, but it is very hard to remove them.

cpolera, 2021-01-16:
Sorry I didnt get back to this sooner. Thats a fair argument. I'd say that my issues may also be in part due to using PETG and the inserts that are not angled along the knurls.

I'm reprinting in ASA now to see if that helps any.

Closed 2020-10-18.

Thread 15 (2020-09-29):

Alternative suppliers for heat inserts?

gawainXX, 2020-09-29:
I've scoured several vendors for the heat inserts in the BoM and haven't had any luck. All of the vendors I've come across didn't ship to the USA or the one that did had them on back order.

I've tried searching for other M3 inserts but none of the ones that I could find had a close outside diameter.

Could you recommend a supplier for the inserts you reference or a compatible alternative that delivers to the USA?

MarMed, 2020-09-29:
I purchased from here awhile back with no issues, and it looks like they
are in stock

https://www.newark.com/tr-fastenings/m3-uhbrhesf/brass-insert-unheaded-m3/dp/46Y7942

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

OmNomNomagon, 2020-10-18:
Thanks Marmed, [Octopart](https://octopart.com/m3-uhbrhesf-tr+fastenings-58189465) also has a good list of available suppliers

monroewilliams, 2021-03-29:
I found something similar on Amazon, which might be easier for some folks in the U.S. https://www.amazon.com/gp/product/B087NBYF65/

Closed 2020-10-18.

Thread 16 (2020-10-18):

New designs improvements for standard hotend, frame

beriberikix, 2020-10-18:
Hello! I printed the original design (all standard core parts) around mid 2019 and have been tracking the changes like cooling fan clearance, x idler, cable connectors, etc. Do you plan to update the "standard" setup eventually?

Thanks!

OmNomNomagon, 2020-10-19:
Thanks for following the project mate. The answer is yes. I've gotten everything working perfectly on the current MK3s / hemera / mk52 version and I'm currently backporting everything to the original frame. I'm not sure on timelines sorry as I also have to convert from tinkercad to fusion for a lot of the parts and its a pain to use with the new file restrictions.

beriberikix, 2020-10-19:
Excellent, that's great to hear! I'm currently using an MK10 (Microswiss all-metal hotend) and would be happy to do any test prints if you need!

beriberikix, 2020-10-24:
What designs can be used with stock without having to do the tedious work of redoing in fusion 360? It seems like the x gantry idler and motor mount will just work? Perhaps putting together a checklist of what's done and what's not done yet would be useful?

beriberikix, 2020-11-01:
FWIW I tried printing the Hemera fan shroud, since it fixes the angle issue, but the mounting hole spacing is different :( I may resort to hacking the model up but I'm not well-versed in Tinkercad (F360 fan myself.)

donjakobo, 2021-02-01:
Any option to share the fusion 360 files? I've mounted a BMG-Wind clone (left handed I believe), replacing the titan aero that was giving me horrible grinding of filament (i wanted a dual geared solution).  Not finding any compatible fans for the new hot end placement (as it shifts slightly up and to the right vs titan aero).

If I could get the Fusion 360 files I would love to take a stab at modifying the existing fan to adjust it.

MarMed, 2021-02-04:
BMG-Wind would be a very welcome addition imo

donjakobo, 2021-02-08:
I've gone and done my best messing with the TinkerCad objects reference to make a workable prototype for the **BMG-Wind** (left handed I believe is the name) that directly replaces the Titan Aero.  I'm going through a coup iterations to get it just right, and just elongate and extend the Titan Aero cooler (rear mounted).

**Key issues:**

1. BMG-Wind Hotend tip is higher (at least for me) than the titan aero, so need to 'shrink' the height of cooler down so it isn't impacting bed
2. BMG-Wind hotend tip is offset so moving the cooler further right and elongating to the front.

OmNomNomagon, 2021-02-11:
> What designs can be used with stock without having to do the tedious work of redoing in fusion 360? It seems like the x gantry idler and motor mount will just work? Perhaps putting together a checklist of what's done and what's not done yet would be useful?

The X gantry parts wont work unfortunately as the rod spacing is different between both printers.  I'm hoping to have a version which will work on both.

xiaoyue, 2021-03-28:
I'm thinking about building the new MK52 frame design, but to keep using the old/original bed and y-carriage. Would it be possible by simply adjusting the Y rod spacing in the new design to be compatible?

OmNomNomagon, 2021-04-07:
> I'm thinking about building the new MK52 frame design, but to keep using the old/original bed and y-carriage. Would it be possible by simply adjusting the Y rod spacing in the new design to be compatible?

Yes, you can use the original heatbed with the MK52 frame design. however you can't use the MK52 bed with the original frame.

iZz0s, 2021-05-25:
are the extrusions for the MK52 edition the same as listed in the BOM?

i've built already a normal core edition and was thinking to reprint the MK52 parts but dont know if it fits with the BOM extrusions, i haven't found other infos.

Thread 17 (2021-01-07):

Hard to follow terminology for MK52 Bed

rogerschlachter, 2021-01-07:
Finally getting around to building this. I appreciate the improved BOM! Thanks. I do however have some questions around some of the instructions...

> ...The Y axis Idler should be mounted 118mm across the front extrusion and the top of the Y motor mount should be 108mm across the rear extrusion. For the MK10 and Titan aero these can be set 10mm further to the right.

The width at this point is 278mm.  278mm / 2 = 139mm to center.  This could be my mistake as I'm reusing my previously printed Y-idler, but it measures 32mm on the top piece of it (part that sits on top of the extrusion). Mounting from the outside edge of the frame to the edge of the top part of it would mean the idler would not be centered on the frame.  And 118 x2 = 236. 278 - 236 = 42.  If I center the idler mount, I have about 123mm from each side.  So some clarity here would be helpful.  Maybe it's just that my previously printed idler is narrower than the current model although it looked the same.

Following that, the Y-motor mount is significantly different than the pictured one. Again, the 108mm from where to where is unclear. A measurement from the outside edge of the frame to the top, flat side of the Y motor mount would be more clear.  The new design doesn't exactly make it obvious where the belt will be once things are mounted and I'd prefer to put off tearing apart my current printer until as late in the process as possible just in case.

Thanks!

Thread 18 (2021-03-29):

Cable Guide Alternate - Motor Mount 360 doesn't fit my X motor

monroewilliams, 2021-03-29:
This part doesn't fit my motor at all. The outside of the motor is approximately 42mm square, and the inside of the square part is about 35mm.

This is definitely the original motor that came on my printer (Monoprice Maker Select v2, purchased in November 2016), but as you can see in the photos it didn't come with a heat sink like the ones shown in the assembly guide. It looks like my motor is a NEMA 17, but this part was designed for a NEMA 14?

This is especially odd since it looks like the hole spacing on the X motor mount I've printed (`X Gantry Motor Mount - MK52 Expansion 360 v2`) seems to have the correct mounting hole spacing for a NEMA 17 motor (31mm).

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

monroewilliams, 2021-04-01:
I see that someone already did a remix to address this:

https://www.thingiverse.com/thing:4590435

so I'll consider this issue resolved.

OmNomNomagon, 2021-04-07:
Thanks for bringing this up mate. I triple checked the part and it looks like I missed a couple of cut operations before i exported the part. I'll have the fixed one uploaded shortly

Closed 2021-04-01.

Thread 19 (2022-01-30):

Guidance for fresh build

DJdaSilva, 2022-01-30:
Hello there! @OmNomNomagon

So I am looking through this repository, keen to build this bad boy!

I realize it is an upgrade over the wanhao i3, actually a total overhaul! I'm really keen to build the full project from scratch, but obviously since I don't have the original printer there are some challenges.... so I guess I am looking for a little guidance on the original printer, small details like stepper motors and electronics etc. Perhaps you know of a clone that would play well with your upgrades? It seems like the wanhao i3 isn't a thing anymore? Am I crazy for wanting to do this as a beginner? I have access to prusa parts so was wondering if their software and electronics could be used with your upgrades to any degree? Anyway sorry lots of questions but any general guidance appreciated!

PS. Thanks for making this public I think it looks amazing!

OmNomNomagon, 2022-03-22:
Hi DJdaSilva,

thanks for your interest in this project. This project can be quite complex if you are not using a Wanhao i3 as a starting point, especially if it is your first build. An alternate option is to start with a Prusa MK3s or clone and do the Zaribo mod.

If you would like to do this project from scratch you will need everything in the build logs along with motors, control board, wiring, and heatbed and a hotend/extruder. I can put together a list together if it is something you would like to persue

Closed 2022-03-22.

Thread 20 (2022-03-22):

MK2A Bed Upgrade?

Iammuffinman225, 2022-03-22:
I seem to recall the MK2A (300x200mm bed) being supported by this repo. Am I mistaken or was it removed as supported build-option?

Rob-Fletcher, 2022-03-22:
I built this a few years back using a 300x200 bed. I have it up on thingiverse (link below). Not sure if thats what you are thinking of. I put all the specs I used in there but this is using older versions of all of the parts so Im not 100% sure my measurements will work anymore. I think they probably should but I havent checked against the newer parts.

https://www.thingiverse.com/make:475171

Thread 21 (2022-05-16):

E3D V6 + Bondtech BMG mounts

rwillsuk, 2022-05-16:
If anyone has made (or could help me make) a mount for a V6 hotend and a BMG extruder, I would be greatly appreciated.

rwillsuk, 2022-05-29:
Found someone that made a modded part. [Here](https://www.thingiverse.com/thing:3994482 )

Closed 2022-05-29.

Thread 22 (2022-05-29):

PSU Mount for plus models

rwillsuk, 2022-05-29:
I created a PSU mount for the plus models to be attached to the z axis frame. [Here](https://www.printables.com/model/216243-reduplicator-mk3x-psu-mount)

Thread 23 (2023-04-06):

Couple of minor issues encountered building with stock MK10

gdewald, 2023-04-06:
First off - thank you for sharing all this incredible work, I can't imagine all the time, effort, and dedication that went into this project!

I just finished a build from my old Maker Select V2 and wanted to share some feedback on the issues I've encountered, hope it is helpful (and I absolutely not intending to share this as criticism, just a few issues I saw following the guide I thought would be helpful to share).

All the issues I encountered appear to be specific to the stock MK10 build and may not be relevant to the other versions in your guide.

Without further ado:

---

[STLs Reduplicator Core Parts/Cable Guide Alternate - Motor Mount 360](https://github.com/OmNomNomagon/ReDuplicator-MK3x/blob/master/STLs%20Reduplicator%20Core%20Parts/Cable%20Guide%20Alternate%20-%20Motor%20Mount%20360.stl)

The bracket opening is ~36mm, but my motor is 42mm. For my build I ended up importing the mesh in Fusion 360 and using it to model a different version to fit my motor.

Comparison of original vs mine below:

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

---

[STLs Reduplicator Core Parts/X Carriage Universal Rear Bearing Plate MK3 V3](https://github.com/OmNomNomagon/ReDuplicator-MK3x/blob/master/STLs%20Reduplicator%20Core%20Parts/X%20Carriage%20Universal%20Rear%20Bearing%20Plate%20MK3%20V3.stl)

The X axis limit switch is meant to be triggered by the notch on this model, however the direction of the notch did not match the orientation of my build (my cable chain and limit switch is on the right side but the notch points left). I attempted to mirror the model and use that instead, however the holes are not symmetrical so this didn't work for me - I ended up retrofitting the [STLs Reduplicator Core Parts/X Carriage Front Extruder Plate MK3 V2](https://github.com/OmNomNomagon/ReDuplicator-MK3x/blob/master/STLs%20Reduplicator%20Core%20Parts/X%20Carriage%20Front%20Extruder%20Plate%20MK3%20V2.stl) mesh in fusion 360 to adjust the mounting holes to fit the mirrored bearing plate.

---

[STLs Reduplicator Core Parts/X Carriage Front Extruder Plate MK3 V2](https://github.com/OmNomNomagon/ReDuplicator-MK3x/blob/master/STLs%20Reduplicator%20Core%20Parts/X%20Carriage%20Front%20Extruder%20Plate%20MK3%20V2.stl)

There is a notch in this model on the side which does not have a corresponding opening in the bearing plate - I'm guessing at some point the motor was intended to be oriented so that the cables were attached from behind the extruder plate? I ended up removing this notch and orienting the motor with wires facing upwards (the notch doesn't cause any issues, just a point of confusion for me).

---

[STLs Reduplicator Core Parts/BLTouch Mount](https://github.com/OmNomNomagon/ReDuplicator-MK3x/blob/master/STLs%20Reduplicator%20Core%20Parts/BLTouch%20Mount.stl)

As the extruder plate had an M3 heatset opening, I installed the heatset first. After I installed the heatset I realize that this would prevent me from being able to use the fastener to tighten the BLTouch mount to the extruder plate.

Usually I see a screw used to join two parts by having a screw pass through a clearance hole of one part into threads of the second part (via heatset), but with this setup I had to hold the BLTouch mount tightly in place while threading the screw through both the m3 heatset and the BLTouch mount in order to get an acceptable fit.

gdewald, 2023-04-20:
Closing as stale

Closed 2023-04-20.

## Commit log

2017-12-13 Create Bill of Materials
2017-12-18 1.0v Final
    Load STLs Golive
    [BLTouch Mount.stl, Base Leg H26.8mm X4.stl, Cable Base Holder.stl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]
2018-01-02 Titan Aero Final Upgrade + Idler Changes for variable z stop mounts
    [Titan Aero BLTouch Mount.stl, Titan Aero X Carriage Front Plate.stl, Titan Aero X Carriage Rear Plate (Same as Original).stl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]
2018-01-11 Part Fan Bracket V1.1 Fix
    Originally loaded an older Part Fan Bracket. the original does not align with the screw holes properly. Please reprint this 1.1 version instead.
    [Part Fan Bracket V1.1.stl, Part Fan Bracket.stl, Titan Aero BLTouch Mount.stl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]
2018-01-29 Y Carriage Belt Holder MK3 Update
    New Y Belt holder based on the MK3 allows for much easier tightening.
    [Y Carriage Belt Holder V1.0.stl, Y Carriage Belt Holder V2.0 Based on MK3.stl]
2018-02-09 Auto stash before merge of "master" and "origin/master"
    [X Gantry Idler 9MM V2.stl, X Gantry Idler 9MM V3.stl]
2018-03-11 Major Update MK3
    New tensioners, carriage, motor mount, extruder spacing, and many build improvements
    [Part Cooling Fan Angled (old).stl, Part Cooling Fan Bracket MK3 V2.stl, Part Cooling Fan MK3 V2.stl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]
2018-03-26 gif sample
2018-05-06 Sensorless Homing Parts for TMC2130s
    [TMC2130 Sensorless Endstop.stl]
2018-08-28 Motor Mount Reverse Config Update
    [X Gantry Motor Mount MK3 V2.stl, X Gantry Motor Mount MK3 V3.stl]
2018-11-04 Prusa MK3 R3 release and improvements
    Updated fan shrouds
    Updated x carriage rear plate
    Updated Z rod securer
    [Part Cooling Fan Bracket MK3 V2.stl, Part Cooling Fan Bracket MK3 V3.stl, Part Cooling Fan MK3 R3 V3.stl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]
2020-02-16 Hemera hotend Upgate
    [ReDuplicator MK3x Expansion - Fan Mount.stl, ReDuplicator MK3x Hemera Fan Shroud.stl, ReDuplicator MK3x Hemera TMC Endstop.stl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]
2020-02-17 Fusion360 Original parts Conversion
    Slowly converting parts across to FUSION 360 as there were reports of inconsistant geometry. Will slowly be updating the rest over time.
    [Base Leg H26.8mm 360 X4.stl, Base Leg H26.8mm X4.stl, Cable Guide Alternate - Motor Mount 360.stl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]
2020-02-17 MK52 Heatbed Expansion Mod
    redesigned parts to allow for the Prusa mk3 MK52 heatbed.
    [Heatbed Cover Bottom MK52 Expansion 360.stl, Heatbed Cover Top MK52 Expansion 360.stl, ReDuplicator MK3x Hemera TMC Endstop 360.stl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]
2020-08-04 Hemera and MK52 update
    Major update of the hemera and MK52 files. Continuing the conversion to fusion 360
    [Base Leg H26.8mm 360 X4.stl, Base Leg X4 360 V2.stl, Hemera BlTouch 360.stl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]
2020-08-04 Relocate alternates
    [X Gantry Cable Box Bottom.stl, X Gantry Cable Box Cover V2.stl, X Gantry Idler Tensioner - MK52 Expansion 360 v2.stl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]
